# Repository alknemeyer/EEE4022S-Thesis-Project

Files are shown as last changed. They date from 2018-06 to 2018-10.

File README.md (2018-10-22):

# EEE4022S Thesis Project: Autonomous Object Identification and Tracking using Neural Networks

Git repository to backup work for my fourth year thesis project at the University of Cape Town. The repo is mostly just to back up my work across multiple work stations, so a lot of the commit descriptions are horrible. Woops.

## Abstract
Many systems require a camera to autonomously identify the objects in its field of view, and then rotate the camera to keep it aimed at a certain class of object.

This report describes the design and implementation of such a system on a low-powered
device. The system uses a Convolutional Neural Network to identify the position of
objects from photos, making use of a neural accelerator device to achieve near real-time
inferences. These measurements are improved through the use of a Kalman Filter, which
estimates the angular state of the tracked object. A multiprocess pipeline is used to
manage the control on a non-real time OS. Finally, a gimbal is designed and built to
rotate the unique payload.

The tracking system is shown to improve over a stationary camera setup.

## Coding style:

I find development using a notebook to be quite a bit easier than developing using a regular python file. Unfortunately, you can't import a `.ipynb` as a module. So, here's the workflow:
1. Use each `.ipynb` file to understand the code and make changes.
2. When you want to commit a change, click `Kernal > Restart and Clear Output` to remove your outputs + make the file a bit smaller (shows up as fewer lines in the git commit).
3. Run the command `jupyter nbconvert --to=python FILENAME.ipynb` to generate a `.py` file which can be imported as a module. Just make sure that any debugging code doesn't run if this is imported as a module into another file!

Alexander Knemeyer

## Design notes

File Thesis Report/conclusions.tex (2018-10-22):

\chapter{Conclusions}

Based on the test results shown in Chapter~\ref{chap:results} and discussion in Chapter~\ref{chap:discussion}, it can be conclusively said that the tracking camera system works better than a stationary camera setup. This is due to three main reasons:

First, the maximum field of view of the tracking system is significantly greater than that of a single stationary camera. One could use multiple stationary cameras, but this comes at a higher cost and extra work on the part of the researchers.

Second, the distortion which arises from setting the stationary cameras to wide-angle mode is significantly higher than the distortion from setting the tracking cameras to an narrow angle mode, which is made feasible by the tracking system. One could counter this buy purchasing even larger numbers of stationary cameras and setting each to the less distorting narrow field of view, but this comes at a higher cost and with extra work on the part of the researchers.

Third, there are other benefits to having a system which aims at a target which aren't practically feasible using a stationary camera setup. For instance, one could attach one or more distance sensors and a GPS to the gimbal to estimate the absolute location of the object.

When viewed as a general tracker in its own right, the system is not perfect and could see significant benefits given an extra week or two of time. The study was also not conclusive in that the tests in the laboratory alone aren't enough to empirically prove that the system could track a fast moving cheetah (given a neural network which can detect one) running close to the camera with a high perceived angular velocity.

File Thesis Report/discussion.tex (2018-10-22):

\chapter{Discussion}\label{chap:discussion}

Some things should be noted when considering the results shown previously.

The first is that, unless one decreased the effects of the image recognition latency, an angle between the cameras orientation and the object will always remain. This can be diminished if one has better knowledge of the animals movement prior to the experiment - for example, if it was known that the only thing being tracked is an object moving from left to right, the yaw Kalman Filter would be able to more reliably predict the current position of the object based on delayed data. This could result in better tracking, but comes with its own problems (such as overshoot if the object slows down, which is part of the RAM groups tests).

The second issue to discuss is that of the maximum angular range of the system, which is limited only by the wiring connecting the stationary part of the tracker to the rotating parts. While the tracker itself has a maximum angular rotation width of 175\textdegree, a portion of the field of view of the camera could be added to this to represent the total range that can be filmed. It may not make sense to add the full width, since part of the premise of the tracker is that object is aimed at directly.

Another topic is the tracking speed of the gimbal, and how it failed to track objects with high a velocity or acceleration. The Kalman Filters noise parameter can be adjusted to vary the state estimate from smoothness as a priority (which could be interpreted as seeing sudden changes in the sensed position as noise, which should be rejected) to robust tracking as a priority (where a sudden change in state is seen as the object moving quickly). In addition, the system would sometimes be unable to track a fast moving object simply due to the gimbals slower rotational rate, which wasn't investigated in time. It is unclear how much the Kalman Filter's parameters and gimbals slow movement limited the performance in this regard.

Finally, all of the tests were performed in a relatively confined space tracking close objects. It is unclear how well the tracker would perform tracking faster objects further away. Based on the results of this report, one could estimate its performance using the formula $\omega = v/r$, where $\omega$ is the rotational velocity, $v$ is the tangential angular velocity and $r$ is the distance to the object. Since the object tracker is confined to track objects at a certain maximum angular rate, but objects themselves move with linear velocities, as long as $\omega$ remains constant between tests on a human in a lab and a cheetah outdoors it is likely that the system would continue to track well.

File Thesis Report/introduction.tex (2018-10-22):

\chapter{Introduction}
This report details the research, design, implementation and testing of an automatic object detection and tracking system. It was made as a part of a final year undergraduate project.

\section{Background to the study}
For years, some researchers have turned to bio-mimicry for insight and inspiration into the design of robots. One such example is the University of Cape Town (UCT) mechatronics laboratory's Rapid Acceleration and Manoeuvrability group, which studies cheetahs with the aim of reproducing their extraordinary manoeuvrability in two and four legged robots \cite{website:uct_mechatronics}. To understand the dynamics of cheetah movement, they require footage of animals as they start and stop a sprint. A requirement of their research is that the cameras must be placed in pairs to achieve depth perception~\cite{website:depth_perception_from_stereo_camera}.

The researchers currently place multiple static cameras, with each pair covering a different area, in order to continuously film an animal through a full sprint. An illustration of this can be seen in Figure~\ref{fig:multiple_gopro_pairs}. \\

\begin{figure}[h!]
  \centering
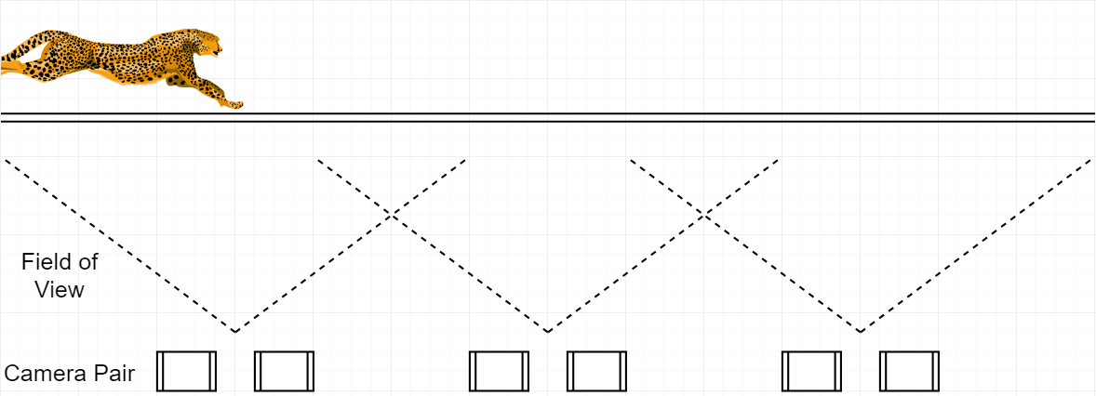
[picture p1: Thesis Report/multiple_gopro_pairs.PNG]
  
  \caption{\label{fig:multiple_gopro_pairs} An illustration of the camera set up in a typical animal movement study. Cheetah clipart from Change.org \cite{website:pic_of_cheetah}.}
\end{figure}

Unfortunately, this setup is not without its disadvantages: having multiple cameras requires extra setup time, effort into synchronizing the footage, money spent on equipment and extra work in keeping all devices charged. To maximise the time spent recording a sprint, the cameras are usually set to wide-angle mode. This introduces distortion into the recordings \cite{website:camera_distorion}.

This resulted in the following question: what if the cameras could instead rotate to track the cheetah as it moves? This way only a single pair of cameras would be required. An illustration of this in two moments of time is shown in Figure~\ref{fig:single_gopro_pair}.

\begin{figure}[h!]
  \centering
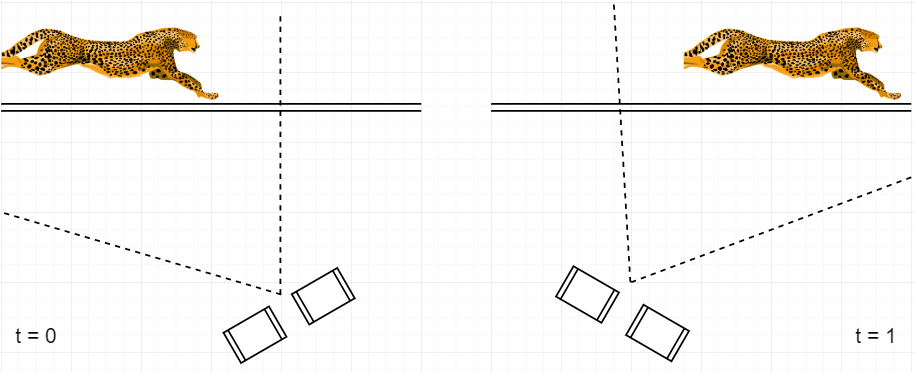
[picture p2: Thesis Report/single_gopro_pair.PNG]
  
  \caption{\label{fig:single_gopro_pair} The proposed solution: a single pair of cameras tracking an animal as it moves.}
\end{figure}

The researchers specified that such a tracking system should,

\begin{itemize}
	\item Not require a beacon, light or any other object to be placed on the object,
	\item Locate the object with high accuracy,
	\item Be able to differentiate between classes of objects, while treating different instances of the same class equally (in other words, locate \emph{any} cheetah regardless of its specific spot pattern),
	\item Have a low enough latency that the object can't escape the field of view of the cameras before a result is reached,
	\item Use a provided Raspberry Pi model 3 B as the main computing platform so as to remain mobile,
	\item Work robustly - this means locating the regardless of its orientation, lighting, specific shape, background, and so on - and finally,
	\item Be able to track any other object with minimal extra work or design required, should the focus of research be changed.
\end{itemize}

After comparing existing object tracking technologies, it was decided that the only way to robustly track the cheetahs in this scenario would be to use a neural network. This decision is elaborated on in section \ref{sec:compare_cv_techniques} of this report. The comparison showed that only machine learning techniques can accurately discriminate between a range of classes of objects using affordable and accessible sensing hardware alone (such as low-cost cameras).

\section{Other object tracking systems}
There are a large number of applications for a system which can track objects in real time using computer vision techniques. Some include:

\begin{itemize}
\item A robot which can sense nearby humans and make sure to not hurt them, or decide on a course of action which depends on the type of object in front of it.
\item A small autonomous airplane which patrols the skies above a national park, and broadcasts the location of any potential poachers that it finds.
\item A camera system which automatically tracks a ball or the centroid of the position all players, helping to record sports games.
\end{itemize}

Object tracking systems have already been incorporated into existing commercial products. One example is the "Mavic" drone from DJI, which can autonomously track humans \cite{website:DJI_mavic}. This allows people to launch the drone and have it autonomously follow them as they move around.

Another example is EyeCloud, a company that has developed a security system which covers a wider area than a single static camera could, and only sends an alert when it detects humans \cite{website:eyecloud}. This prevents false alarms from sounding when safe classes of objects, such as dogs, enter the field of view.

\section{Objectives of the study}
Based on the problem stated by the UCT researchers, the objective of the study is to design, build and test a system which can autonomously identify and track a fast-moving object using modern computer vision methods. A successful design would be able to rotate a pair of cameras to continuously aim at an object, track the object for longer than a stationary camera pair could, and not require the cameras to be set to distorting wide-angle modes.

Note that, while the ability to autonomously track an object has a wide range of applications, it is useful to limit oneself to a particular need in order to produce quantifiable 'success or failure' metrics. Thus, this project and report are mainly about solving a specific issue, with the premise that the project can be used for other applications with minimal modification. Discussions on literature and other applications will treat the system as a general purpose object tracker.

\section{Scope and limitations}
Due to the limited time and finances in an undergraduate thesis, testing the tracking system on actual cheetahs was not part of the agreed scope of this project. Instead, it was tested on moving humans in complex environments with the hope that this sufficiently mimics the scenario of tracking cheetahs (or any other fast-moving object) in the wild.

Additionally, the study was limited to tracking only one object in the frame at a time. This is because it is not immediately obvious what should be done when more than one object is present in the frame.

\section{Plan of development}
A development schedule was devised to decide how much time could be allotted for each component of the final system. It was as follows,

\begin{enumerate}
\item Create a rough design for the system as a whole to understand which skills and components would be necessary.
\item Spend a month learning relevant new theory, mostly in the field of computer vision.
\item Set up the main computing platforms, installing relevant software and testing the camera module, over the course of a week.
\item Optimize a cutting edge neural network for the specific scenario in this project over the course of two weeks. Failing that, choose an existing neural network architecture.
\item Compile the neural network and deploy it onto a neural accelerator stick, writing appropriate software, over the course of a week.
\item Use two weeks to design and 3D print a camera gimbal, and procure the necessary controller and actuators.
\item At the same time, rewrite the gimbal controller communication standard in python to allow the raspberry pi to send and receive commands.
\item Spend a week modelling the expected movement of the tracked object, and designing and implementing an appropriate Kalman Filter. Update this based on preliminary test results.
\item Spend two weeks implementing a parallel process-based data pipeline which takes a photo on the Pi camera, pre-processess it, passes it through the neural accelerator, retrieves the results, passes the results into the Kalman Filter and then commands the gimbal motors to re-orient the camera appropriately. 
\item Test final the system over the course of a week, tweaking the design based on results.
\item Use the last three weeks to write a report which summarizes the entire project, based on small notes taken during the course of the project.
\end{enumerate}

\section{Report outline}

The report begins with a review of the current literature surrounding object tracking. As the system combines a number of technologies, it also presents previous knowledge on all of the components which ultimately formed a part of final system.

Next, a more detailed description of the problem, plan of action, activities and project timeline are provided.

Following that are a few chapters which discuss the actual methodology used in the design and implementation of the tracking system. This is done with the aim that reproducing and extending the project can be done with minimal effort.

The results of testing the system are then shown.

Finally, the report ends off with conclusions on the project's success or failure, along with recommendations for future work.

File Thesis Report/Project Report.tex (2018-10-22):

\documentclass[a4paper,12pt]{report}

\usepackage[top = 1in, bottom = 1in, left = 1in, right = 1in]{geometry}
\usepackage{graphicx}
\usepackage{fancyhdr}
\usepackage{amsmath, amsthm, amssymb}
\usepackage{lastpage}
%\usepackage{subfigure}
\usepackage{lscape}
\usepackage{hyphenat}
\usepackage{setspace}
\usepackage{hyperref}  % used for \href and urls in .bib
\usepackage{xcolor}  % use to colour text
\usepackage{subfig}  % putting packages side by side
\usepackage{textcomp} % degree symbol

%\usepackage{listings}
\usepackage{pythonhighlight}
%\begin{python}
%x = 1
%\end{python}
%\pyth{__init__}

\usepackage{sectsty} % adjust size of chapter headings
\chapternumberfont{\large}
\chaptertitlefont{\Huge}

\usepackage{wrapfig} % wrap text around figures
%\begin{wrapfigure}{R}{5.5cm}
%\caption{A wrapped figure going nicely inside the text.}\label{wrap-fig:box_around_blossom}
%\includegraphics[width=5.5cm]{methodology/box_around_blossom}
%\end{wrapfigure}

\usepackage{titlesec} % decrease the whitespace at chapter start
\titleformat{\chapter}[display]
{\normalfont\large\bfseries}{\chaptertitlename\ \thechapter}{0pt}{\Huge}
\titlespacing*{\chapter}{0pt}{-40pt}{5pt}
%	  {shift right/left}, {up/down}, {between title and text}

%\usepackage{animate} % embed videos

% add lines by header and footer
%\usepackage{titleps}
%\newpagestyle{ruled}
%{\sethead{}{Header}{}\headrule
%  \setfoot{}{Footer}{}\footrule}
%\pagestyle{ruled}

%%%%%%%%%%%%%%%%%%%%%%%%%%%%%%%%%%%%%%%%%%%%%%%%%%%%%%%%%%%%%%%%%%%%%%%%

% page formatting
\parskip = 4mm
\parindent = 0mm
\renewcommand{\headrulewidth}{0.4pt}
\rhead[]{\thesection}
\lhead[\thechapter]{}

%%%%%%%%%%%%%%%%%%%%%%%%%%%%%%%%%%%%%%%%%%%%%%%%%%%%%%%%%%%%%%%%%%%%%%%%

\begin{document}

\thispagestyle{empty}
{\Huge \begin{center}
Autonomous Object Identification and Tracking using Neural Networks% title
\hrule
%{\Large ya boi} % subtitle
\end{center}}

\vskip 5mm
\begin{center}
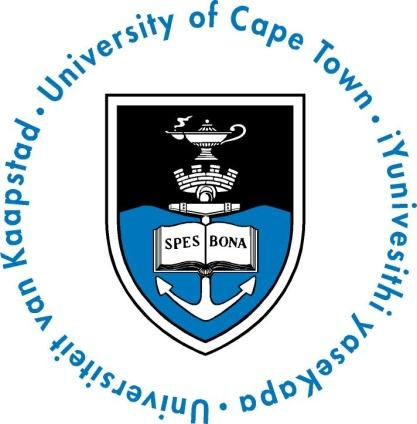
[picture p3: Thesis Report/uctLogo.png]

\end{center}

\vskip 5mm
\begin{center}
\textbf{Presented by:}\\
Alexander Lutz Knemeyer\\
KNMALE002\\
Department of Electrical and Electronics Engineering\\
University of Cape Town
\end{center}

\vskip 10mm
\begin{center}
\textbf{Prepared for:}\\
Callen Fisher and Edward Boje \\
Department of Electrical and Electronics Engineering\\
University of Cape Town
\end{center}

\vskip 10mm
\begin{center}
Submitted to the Department of Electrical Engineering at the University of Cape Town in partial fulfilment of the academic requirements for a Bachelor of Science degree in Mechatronics Engineering
\end{center}

\vskip 5mm
\begin{center}{\bf \today}\end{center}

{\centering
\textbf{Key words:} object tracking, autonomous, neural network, Kalman Filter, multiprocess}

\newpage

%\thispagestyle{empty}  % leave a blank page
%\mbox{}
%\newpage

\onehalfspacing
\nohyphens{
\thispagestyle{empty}
\vskip 40mm

% Please leave the declaration as it is (Standard UCT declaration).
{\Large Declaration} \\
\hrule

\vskip 10mm
\begin{enumerate}
\item I know that plagiarism is wrong. Plagiarism is to use another's work and pretend that it is one's own.
\item I have used the IEEE convention for citation and referencing. Each contribution to, and quotation in, this report from the work(s) of other people has been attributed, and has been cited and referenced.
\item This report is my own work.
\item I have not allowed, and will not allow, anyone to copy my work with the intention of passing it off as their own work or part thereof.
\end{enumerate}

\vskip 10mm
Signature: \ldots\ldots\ldots\ldots\ldots\ldots\ldots\ldots\ldots
\\A. L. Knemeyer
\vskip10mm
Date: \ldots\ldots\ldots\ldots\ldots\ldots\ldots\ldots\ldots\ldots

\fancyfoot[C]{\thepage}
\pagestyle{plain}
\newpage

\pagenumbering{roman}
{\Large Acknowledgements} \\
\hrule

A number of people were immensely helpful in the undertaking of this project.

Callen, thank you for your guidance, encouragement and supervision.

Justin, thank for your endless patience and advice whenever I came with questions or asking for a favour.

Stacey, thank you for laser cutting components for the gimbal. You're far too nice.

Neil, thank for proofreading an earlier version of this report. Your input was highly appreciated and raised the quality of my writing.

Sylvan, your friendship during this trying time truly saved my sanity. I'll always fondly remember working in the lab with you.

My family, your confidence in me and my abilities greatly helped keep my ambitions high and stress at a manageable level.

Sophia, thank you for your endless support and encouragement. I don't handle stress very well so our little chats helped a lot with my sanity.

\newpage

\include{abstract}

{\Large Abbreviations and Initialisms} \\
\hrule
\begin{table}[h!]
	\centering
	\begin{tabular}{p{2cm} p{0.1cm} p{15cm}}
	FOV & & Field Of View \\
	CNN & & Convolutional Neural Network \\
	NCS & & Neural Compute Stick \\
	OS  & & Operating System \\
	VM  & & Virtual Machine \\
	CPU & & Central Processing Unit \\
	GPU & & Graphics Processing Unit
	\end{tabular}
\end{table}

\newpage

\tableofcontents

\newpage
\listoffigures

% Page formatting, to place section titles as headers of odd pages and Chapter titles as headers of even pages.
\newpage
\fancyhead[RE,LO]{}
\fancyhead[LE]{\leftmark}
\fancyhead[RO]{\rightmark}
\pagestyle{fancy}

\pagenumbering{arabic}

%%%%%%%%%%%%%%%%%%%%%%%%%%%%%%%%%%%%%%%%%%%%%%%%%%%%%%%%%%%%%%%%%%%%%%%%

\include{introduction}
\include{literature_review/literature_review}
\include{literature_review/lit_nn}
\include{literature_review/lit_EKF}
\include{literature_review/lit_gimbal}
%\include{literature_review/lit_controller}
%\include{research_design_and_timeline}
%\include{Methodology}
%\include{methodology/meth_system}
\include{methodology/meth_nn}
\include{methodology/meth_EKF}
\include{methodology/meth_gimbal}
\include{methodology/meth_control}
\include{results/results}
\include{discussion}
\include{conclusions}
\include{recommendations}
%\include{References}
%\appendix
\chapter{Appendix}
The authors submission into the SAIEEE NSPC:

\href{https://www.youtube.com/watch?v=NjCOmwhG3zo}{\pyth{https://www.youtube.com/watch?v=NjCOmwhG3zo}}
\\

Two videos which compare the stationary and tracking cameras:

\href{https://youtu.be/Oea_mKTjV5U}{\pyth{https://youtu.be/Oea_mKTjV5U}}
\\

The GitHub page containing all code:

\href{https://github.com/alknemeyer/EEE4022S-Thesis-Project}{\pyth{https://github.com/alknemeyer/EEE4022S-Thesis-Project}}

\newpage

\bibliographystyle{IEEEtran}
%\bibliographystyle{plain}
\bibliography{references}

}
\end{document}

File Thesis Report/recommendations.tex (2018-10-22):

\chapter{Recommendations}

There are a number of alternative ideas and approaches which merit investigation. The ideas were left unimplemented as they were realised too late in the process or would have required too much time or money.

The list of future recommendations is as follows:

\begin{enumerate}
	\item Instead of tracking the state of the object as an angle, try instead track it as an $(x,~y)$ position on a plane surrounding the tracker. This would either require a depth estimating neural network or a distance sensor which works even when the system doesn't aim directly at the object.
	\item Get a camera, computer and neural accelerator which decrease the total sensing latency.
	\item Consider adding an encoder to the gimbal to avoid built up gyroscope drift when an accelerometer axis lines up with with a rotation axis.
	\item Consider switching the main programming language from python to something faster and better oriented to parallelism. The language could also be low-level, now that most of the debugging and prototyping has already been done.
	\item After the network selection process occurred in this project, the TinyYOLO architecture was added to the list of models officially supported by the Movidius NCS. TinyYOLO has some grand claims about its speed, so it should be evaluated as option for future work. Reducing the latency in the system would make the overall project significantly easier.
\end{enumerate}

%Bad things from gimbal: hard to make screws firm+they come loose, didn't make a nice way of keeping cameras inside frame, didn't make nice spot to put pi and gimbal controller.

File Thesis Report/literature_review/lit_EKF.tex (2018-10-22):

\section{The Kalman Filter}

While object detection algorithms operate at rates of less than 10 Hz when run on the Movidius NCS, the controller for a rotating camera necessitates a higher frequency. In addition, it would be useful to be able to estimate a likely position for the object in cases where the object detection algorithm fails.

The Kalman Filter (and its nonlinear variant, the Extended Kalman Filter), can solve both of these problems \cite{kalman1960new}.

\subsection{An brief introduction to the Kalman Filter}
A Kalman Filter is an algorithm used to estimate the state of a linear system ($\hat{x}$) along with the uncertainty of the estimate ($P$) based on measurements over time ($z$). The measurements are assumed to include noise with covariance $R$. It makes use of a model ($F$) which represents the dynamics of the system ($\hat{x}_{k} = F\hat{x}_{k-1}$), along with a matrix which represents inaccuracies in the model, dubbed 'process noise' ($Q$) and measured factors which affect the state, but aren't part of the current set of states ($u$). It takes into account the sensor scaling which maps between sensor measurements and state values ($H$). The notation for Kalman Filters has not been totally standardised.

A variety of excellent resources exist which explain the deeper intuition behind the Kalman Filter \cite{website:wlu_kalman_tutorial, website:bzarg_kalman_tutorial}. Thus, only the equations and high-level concepts which are absolutely necessary will be discussed in this chapter.

Kalman Filters continuously alternate between a predict stage and an update stage. In the predict stage, the Kalman Filter uses a model of the system and known disturbances to update the state estimate and uncertainty estimate. These are represented by the equations,

\[ \hat{x}_k = F_k \hat{x}_{k-1} + B_k u_k \]
\[ P_k = F_k P_{k-1} F_k^T + Q_k \]

The $k$ subscripts denote the point in time at which the calculation takes place. This means that any matrix in the algorithm could be updated as time goes on.

In the 'update' stage, the Kalman Filter makes use of a model of uncertainty estimates to produce a new state estimate which is a trade-off between new data from a sensor, and the state estimate produced by the predict stage.

\[ \hat{x}_k = \hat{x}_{k-1} + K_k (z_k - H_k \hat{x}_{k-1}) \]
\[ P_k = (I - K_k H_k) P_{k-1} \]

where the Kalman gain $K$ at a time $k$ is calculated as,
\[ K_k = P_k H_k^T (H_k P_k H_k^T + R_k)^{-1} \]

%These stages are alternated as \emph{predict} $\rightarrow$ \emph{update} $\rightarrow$ \emph{predict} $\rightarrow$ \dots
As an illustration, consider the extremes during the update stage: when $K = 0$, we have

\[ \hat{x}_k = \hat{x}_{k-1} + 0 (z_k - H_k \hat{x}_{k-1}) = \hat{x}_{k-1} \]

If $H_k = 1$ and $K = 1$, we have

\[ \hat{x}_k = \hat{x}_{k-1} + (z_k - \hat{x}_{k-1}) = z_k \]

Values of $K$ in between result in a state update which is some combination of the sensed values and modelled dynamics of the system. The Kalman Filter selects this combination based on its estimate of the mean and variance of the state estimate and measurement. An illustration of this is shown below, in Figure~\ref{fig:kalman_filter_loop}.

\begin{figure}[h!]
  \centering
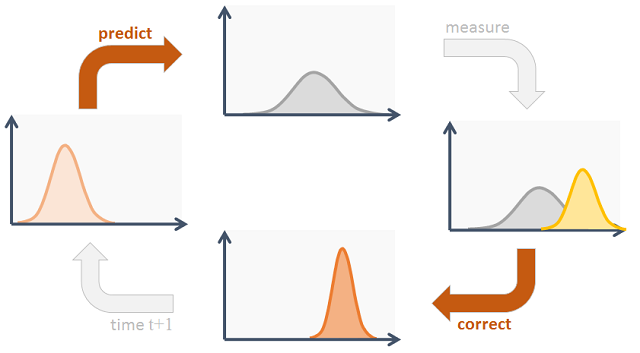
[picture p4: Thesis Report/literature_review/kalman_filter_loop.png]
  
  \caption{\label{fig:kalman_filter_loop}An illustration showing how the mean and covariance of an estimate (as predicted by the Kalman Filter) changes during the predict and update stages \cite{website:kalman_visualisation}.}
\end{figure}

Finally, given a Kalman Filter with an accurate estimation of the systems state and a model which adequately predicts the future state of the system, one can interpolate between readings from a sensor with slow update rates by making use of the prediction model $F$. This could mean getting model updates at a required speed of 20 Hz using a sensor which only makes measurements at a rate of 5 Hz.

\subsection{An introduction to the Extended Kalman Filter}
An Extended Kalman Filter (EKF) is simply a nonlinear version of a Kalman Filter, where the transition from estimated state $\hat{x}_{k-1}$ to state $\hat{x}_k$ is some nonlinear mapping $f(x)$ and/or the mapping from state values to sensor values is a nonlinear function $h(x)$. It works by using a Taylor approximation to linearize about an estimate of the current mean and covariance. This also results in differing values for the sensors Jacobian, $H~=~\frac{\delta h}{\delta x}$.

\[ F \hat{x} \rightarrow f(\hat{x}) \qquad H \hat{x} \rightarrow h(\hat{x}) \]

To understand the effects of this, consider the following: given a sensor which maps from state to measurement following the function $h(x) = x^2 - 10\cos{(x)}$, reading a value of $x = 8.5$ when the state was actually $x=7.5$ would result in an absolute error of $25.5$. However, reading a value of $x=4.5$ when the state was actually $x=3.5$ would result in an absolute error of $0.743$. Clearly, the same one unit error (due to noise, for example) should be treated differently depending on where it happens on the sensor curve. The EKF does just this! Code to create the plot can be found on the authors \href{https://github.com/alknemeyer/EEE4022S-Thesis-Project/blob/master/Final%20code/Illustrations%20for%20report.ipynb}{GitHub repository}.

\begin{figure}[h!]
  \centering
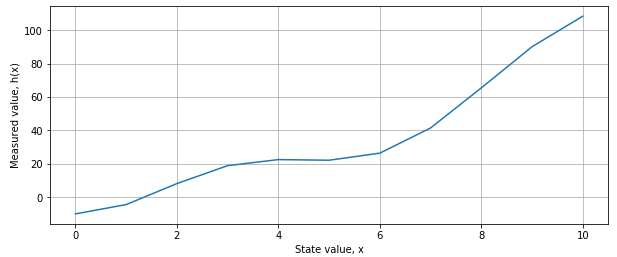
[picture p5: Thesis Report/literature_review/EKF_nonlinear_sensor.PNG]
  
  \caption{\label{fig:EKF_nonlinear_sensor}A plot of a hypothetical nonlinear sensor which maps state to measured value according to the function $h(x) = x^2 - 10\cos{(x)}$.}
\end{figure}

Thus, an EKF would update its covariance estimates in a different way depending on the part of the sensor/prediction curve it finds itself on. Implementation-wise, the only difference between the linear and non-linear variants of the Kalman Filter is that the state transition and observation models can be non-linear differentiable functions with a constantly updating sensor Jacobian.

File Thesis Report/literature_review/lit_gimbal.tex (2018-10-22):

\section{The camera gimbal}
A gimbal is device which can rotate about one or more axis \cite{website:definition_gimbal}. A typical use is to place a camera and 3 actuators on a gimbal, resulting in the ability to rotate the camera in the roll, pitch and yaw axis. An annotated render of this can be found in Figure~\ref{fig:roll_pitch_yaw_camera}.

\begin{figure}[h!]
  \centering
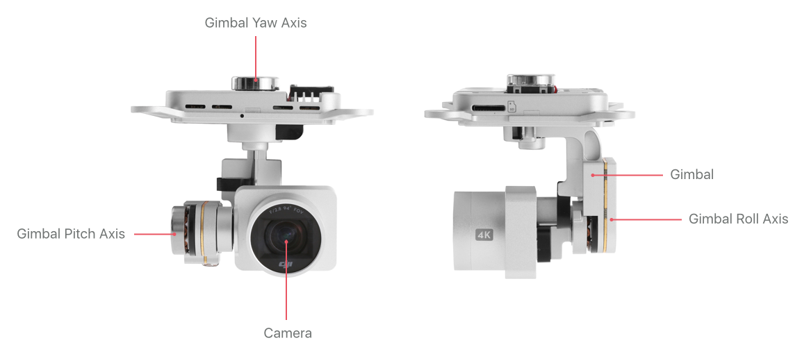
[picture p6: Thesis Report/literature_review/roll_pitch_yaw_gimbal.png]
  
  \caption{\label{fig:roll_pitch_yaw_camera} An illustration of the roll, pitch and yaw axis used in a gimbal~\cite{roll_pitch_yaw_camera}.}
\end{figure}

While gimbal designs are \emph{fairly} standard, a few critical design choices must be made when building or buying one.% The rest of this chapter will detail some of the options available.

\subsection{Comparison of actuator types}\label{ssec:gimbal_comparison}
The type of actuator used in the gimbal has a significant effect on the design of the gimbal (due to actuator shape), the speed it can move, the camera weight it can handle and quality of the resulting photos and videos (due to actuator vibrations). Thus, three relevant actuator types (a brushed DC motor, a servomotor and a BLDC motor) were considered and compared, taking into account the selection available at local stores.

To make the comparison more concrete, specific possible models were chosen. The DC (Direct Current) motor considered was 99:1 Metal Gearmotor available from Pololu.com \cite{DC_motor_choice}. The servo motor was a 20kg.cm Metal Gear Servo available from Robotics.org.za \cite{servo_motor_choice}. Finally, the Brushless DC (BLDC) motor was a Quanum 2208 brushless gimbal motor \cite{bldc_motor_choice} available second hand.

The DC motor is relatively long and heavy. It also requires an additional H-bridge circuit to drive it. Finally, it wasn't clear how the Raspberry Pi (running a non realtime OS) would use the rotational decoder and apply a control law.

The servo motor is relatively easy to use as the Raspberry Pi has built in PWM. It also has relatively high torque. However, it too is relatively large and would likely move in a jittery fashion, resulting in lower quality footage.

Lastly, the BLDC motor is potentially expensive and quite complex to use. Its advantages are its was compactness, low weight and high speed. It is worth noting that, while controlling BLDC motors can be fairly complex, using a store-bought controller allows for one to easily leverage off the design work of other engineers. This results in a faster, smoother and more stable gimbal than one could build in a short period of time.

\subsection{\label{ssec:gimbal_design_inspirations}Gimbal design inspirations}
It is useful to review existing gimbal designs in order to avoid unnecessary re-invention of the wheel. Luckily, a large number of designs are available on the internet. One design which stood out from the research phase was \href{https://www.thingiverse.com}{thingiverse.com} member Velocirotor's clever gimbal design, dubbed the \href{https://www.thingiverse.com/thing:2804872}{Primbal Session} \cite{website:primbal_session}. It is light-weight, simple to 3D print and has an easy method to adjust length to balance the gimbal's three axis. A render of the design can be found in Figure~\ref{fig:primbal_pic}.

\begin{figure}[h!]
  \centering
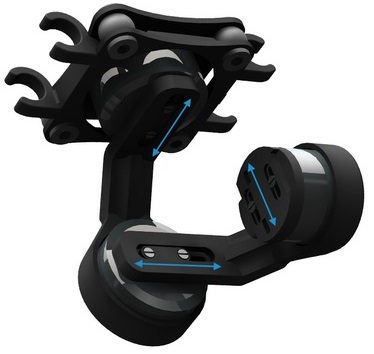
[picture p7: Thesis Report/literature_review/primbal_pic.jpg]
  
  \caption{\label{fig:primbal_pic} A render of the Primbal Session gimbal design.}
\end{figure}

Some inspiration was also taken from a gimbal designed by mechatronics engineering student Sylvan Morris, made during a period of vacation work. Noteworthy characteristics include the two-plate shock absorption system and method of mounting onto a quadcopter. A photo of his design can be found in Figure~\ref{fig:sylvan_gimbal}.

\begin{figure}[ht!]
  \centering
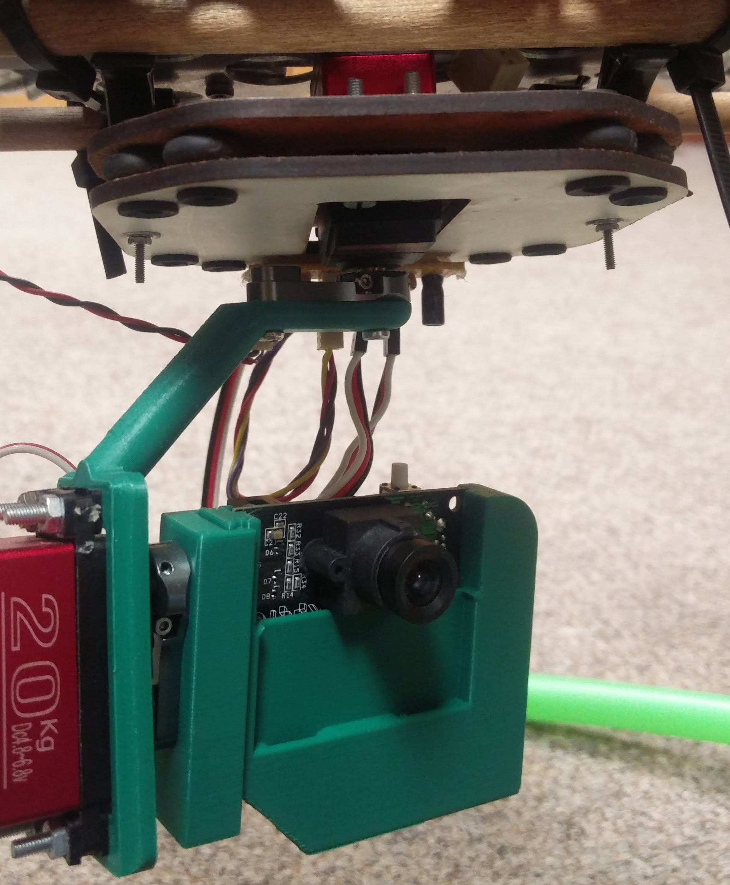
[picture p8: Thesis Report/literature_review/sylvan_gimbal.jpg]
  
  \caption{\label{fig:sylvan_gimbal} A photo of Sylvan Morris's gimbal design.}
\end{figure}

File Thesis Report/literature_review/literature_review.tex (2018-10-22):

\chapter{Literature Review}

The design of a real time object tracker on a low-power computer necessitates several systems, including object detection, a camera gimbal and a Kalman Filter. The literature relevant to these systems are covered in more detail in this chapter.

\section{An overview of real time computer vision based automatic tracking systems}\label{sec:compare_cv_techniques}
The mechatronics RAM group researchers required a system which can track an object using a camera and computer vision techniques alone. That requirement is somewhat heavy on jargon, but it can be unpacked as follows:

\textit{Track: follow the trail or movements of (someone or something), typically in order to find them or note their course \cite{website:definition_track}.}
%
A number of systems which interact with the world must track an object. To give some examples, in our daily lives we as humans visually track other cars when driving, keep an idea of our geographic location and estimate the position and velocity of people as they walk so we don't bump into them. Examples more relevant to this project include pointing camera at a ball during a sports match and tracking poachers from the air in a game park.

\textit{Automatic: working by itself with little or no direct human control \cite{website:definition_automation}.}
%
A human could (in principal) manually track an object using their own vision and natural object-recognition ability. However, this isn't feasible for all applications: this type of job can be fairly boring, resulting in the human losing concentration over time. Another issue is that the human should be paid to perform this task if it is their job. This completely excludes all applications which must have a low running cost.

In contrast, autonomous tracking systems require little to no ongoing human work - as a result, they tend to have vastly reduced running costs with higher reliability over long run times \cite{website:BCG_automation}.

\textit{Real time: relating to a system in which input data is processed within milliseconds so that it is available virtually immediately as feedback to the process from which it is coming, e.g. in a guidance system \cite{website:definition_real_time}.}
%
Not all tracking systems can (or need to) run in real time. For example, one might film a moving object and then automatically locate the objects position in the video offline. However, certain systems must track an object in real time so as to be able to (for example) orient a camera to point at the object, or result in some other immediate response.

\textit{Computer-vision: a field of computer science that works on enabling computers to see, identify and process images in the same way that human vision does \cite{website:definition_computer_vision}.}
%
Some tracking systems require a device to be placed on the object being tracked. Some still require a camera - for example, one could place an infra-red beacon on the object and pair it with a camera with an appropriate lens \cite{koyuncu2010survey}. Others involve no cameras, and instead use embedded sensors alone (such as GPS, accelerometers and gyroscope) \cite{sakpere2017state}. Again, while this may be acceptable for some systems, it comes at a cost: some sort of device must be placed on the object. If the object is a cheetah, this could cause a disturbance to the animals behaviour. The device must be kept charged, so periodic interference with the object is required. Physical contact must be made with the object to install the tracker - this isn't always possible.

In contrast, object tracking based on computer vision doesn't require any device to be placed on the object. This is far more scalable, as the same system can track more objects without any additional hardware. Embedded tracker based systems require an additional piece of hardware for every object being tracked.

However, these benefits come at a cost: the object must be close enough to the camera system that the object can be recognised. In contrast, an embedded GPS, IMU and radio system could track objects to the range of the radio system, provided at GPS lock can be achieved.

%https://en.wikipedia.org/wiki/Infra-red_search_and_track
There are other vision-based systems which don't use computer-vision techniques. For example, infra-red tracking systems don't usually differentiate between classes of objects, but instead track any movement in the frame \cite{sakpere2017state}. These systems are often relatively cheap, but since they can't differentiate between types of objects, they don't work for all scenarios. Another issue is that heat-based systems stop working when the external temperature is the same as the temperature of the object being tracked. This is an issue for a system which might track a human with a body temperature of 37.5\textdegree{} in 37\textdegree{} weather.

Finally, there are other systems which can track objects without embedding a tracker or using vision. Technologies like radar can send off a ping and then build a view of the environment based on the returning signal \cite{sakpere2017state}. Radar tends to give good range (significantly further than vision would give), but struggles to differentiate between types of objects very well. For example, a radar system \emph{might} be able to differentiate between a car and a human from 1km away, but not human from a dog or car from elephant. It also doesn't work well at closer distances, and often has a prohibitive cost.

Of course, there are reasons for and against the use of each of these technologies. These should be considered before deciding on a particular approach for a given project.

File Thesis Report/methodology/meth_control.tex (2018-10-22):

\chapter{Control Loop Design and\\Implementation}
This chapter details the process of combining the project components mentioned in previous chapters. This was surprisingly non-trivial due to the high latency of the object detector and need for parallelization.

\section{Description of software implementation}
The main negative consequence of choosing a CNN for object detection is the latency introduced by the long inference time. This influenced the system design to a great extent. In addition, the unexpectedly long time required to get a photo from the Pi camera and preprocess it added to the list of compute-intensive latency-causing components. Thus, it was decided that the system would make use of multiprocessing and message passing, made possible and simple through the use of python's built in \pyth{multiprocessing} module.

This helped in two ways: the first is that it freed the main process to continuously send commands to the gimbal using the estimate from the KF. It would simply not be tolerable to be out of this loop for 200ms or more while a photo is taken and the result inferred.

The second advantage is that while implementing a parallel data pipeline would increase the overall latency between a photo being taken and the result being used, the number of readings per second actually increases. This is because while one process takes a photo, another can simultaneously infer the image while the parent process communicates with the gimbal controller. This meant that a single faulty or missing measurement would quickly be replaced by a new one.

Thus, data was passed from one process to the next using parallel processing Queues. A block diagram of this and the other components in the pipeline is shown in Figure~\ref{fig:system_block_diagram}.

\begin{figure}[h!]
  \centering
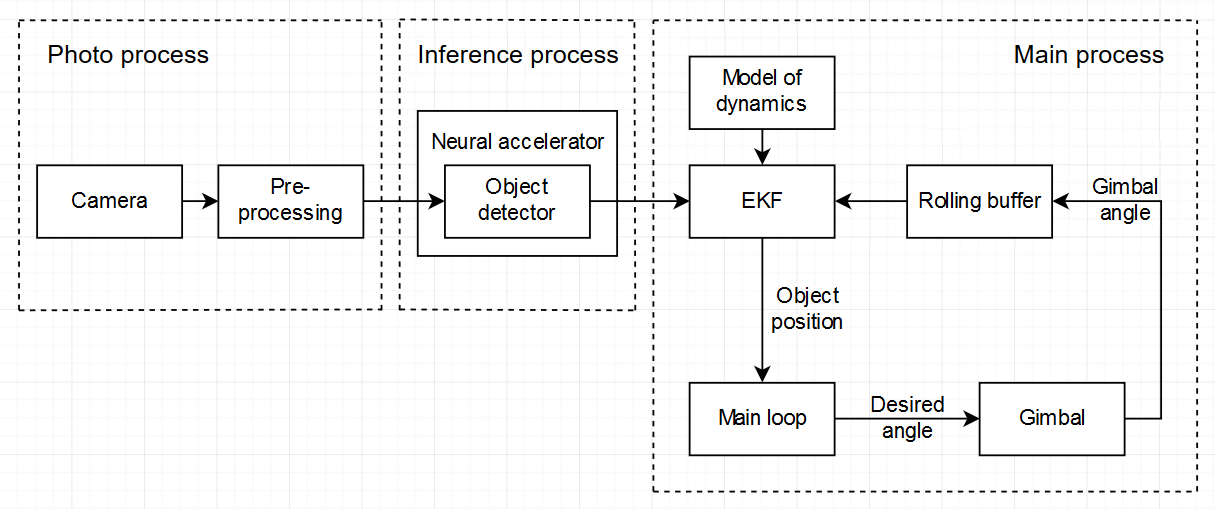
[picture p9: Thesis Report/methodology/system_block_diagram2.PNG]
  
  \caption{\label{fig:system_block_diagram}A block diagram of the flow of data through the system, showing the functions of each process.}
\end{figure}

A more detailed description of the rest of the general flow diagram and the reasoning behind the choices made is detailed in the following subsections.

\subsection{The photo process}
In the photo stage, a child process would interface with the Raspberry Pi camera. It received all photos taken, did some preprocessing on each image, and then passed the resulting array to the next stage in the pipeline. It also sent the time at which the photo was taken. A single loop in this stage took around 60-150ms, depending on the chosen camera resolution.

\subsection{The inference process}
In the inference stage, another child process interfaced with the Movidius NCS. It received the preprocessed images from the previous stage and loaded them onto the neural accelerator. While waiting for the inference result, it would occasionally save a copy of the photo to disk for offline debugging purposes. Once it received the result, it would decode the neural net output, put it and the photo time into an easy to use python dictionary and place it in a final buffer. Again, this needed to be in a separate process as the total time required to pass an image to the NCS and then infer a result was about 100ms.

\subsection{The main process}
While this was happening, the main parent process continuously ran a control loop which received the results from the inference process, and used it to update two Kalman Filters which track the object's pitch and yaw states. It also communicated with the gimbal controller using its serial API. Lastly, it logged relevant data for debugging purposes.

\section{Fixing timing issues}
The large latency in the object detection caused further problems which needed to be fixed. These problems and their solutions are described in the following subsections.

\subsection{Inference result/gimbal state timing issues}
Recall that the neural network can only give a relative angle between the camera and the object, while the gimbal works using absolute angles with respect to some initial position.

The Kalman Filters, each tracking the absolute angular states of the object, would need to be passed the results from the neural network as absolute angles. This could be done by reading requesting the gimbal to send its angular position at the time that the photo was taken. \\

\begin{python}
camera_angle = gc.get_motor_angles()
KF_yaw.update(angle_to_object_yaw + camera_angle['yaw'])
KF_pitch.update(angle_to_object_pitch + camera_angle['pitch'])
\end{python}

However, this presented a new problem to be solved - the angular state of the camera at the time that the photo was taken usually significantly different by the time the result had been inferred due to the large latency in the inference.

\begin{enumerate}
\item $t = 0$: photo taken and inference started.
\item $t = 200ms$: result received for for $t=0$. By this time, the gimbal has moved slightly, causing a mismatch between the relative angles from the recent inference and the current absolute gimbal angles.
\end{enumerate}

The solution was to keep a rolling buffer of a few gimbal angle readings, and then use the angle measurement at the time closest to the photo time to properly convert the neural network measurement from a relative angle to a global one. The snippets of code relevant to this are shown below. \\

\begin{python}
# gc_angles is the dictionary returned from gc.get_motor_angles()
def log(self, gc_angles):
	self.time_buffer[self.idx % self.buffer_len] = time.time()
	self.yaw_buffer[self.idx % self.buffer_len] = gc_angles['yaw']
	self.pitch_buffer[self.idx % self.buffer_len] = gc_angles['pitch']
	self.idx += 1

def angle_closest_to(self, photo_time):
    # index of time closest to the photo time
    idx = np.argmin(np.abs(self.time_buffer - photo_time))
    return self.yaw_buffer[idx], self.pitch_buffer[idx]

# log angle of gimbal
gimbal_buffer.log(gc.get_motor_angles())

# later on, when a result arrived from the neural network:
obj_yaw, obj_pitch, photo_time = get_angles_and_photo_time_from_nn()
logger_yaw, logger_pitch = gimbal_buffer.angle_closest_to(photo_time)
EKF_yaw.update(obj_yaw + logger_yaw)
EKF_pitch.update(obj_pitch + logger_pitch)
\end{python}

Another reason why this approach was necessary was because the time between taking a photo and getting the result was non-constant.

\subsection{Control timing issues}
Given that the KF in the gimbal was working correctly, there were two options for how to handle the latency of the pipeline.

\begin{enumerate}
\item $t = 0$: photo taken and inference started.
\item $t = 200ms$: result received for for $t=0$. By this time, the object has moved slightly.
\item Two options to move the gimbal at $t=200ms$:
	\begin{itemize}
	\item Use the KF estimate using measurements from $t\le0$.
	\item Use the KF to predict from $t=0$ to $t=200ms$
	\end{itemize}
\end{enumerate}

The first approach was to track the KFs estimate of the object at all times. Since the KFs receive all data with a roughly $\approx 200ms$ delay, the resulting system would essentially track the position of tracked object $200ms$ in the past. This approach accepts the fact that the camera will usually not aim at the camera but instead lag a few degrees behind it (depending on the angular velocity of the object).

The second approach would be to use the KF estimate of the angular state of the object to 'predict' from the KF's $\approx 200ms$ lagging time into the actual live time. If successful, the camera would perfectly track the position of the object as it moves along. However, there is no guarantee that the KF prediction will match the actual movements of the object. Thus, this approach would be prone to things like extreme overshoot every time the object slowed down or turned around.

There is merit to both approaches - the first is more robust, with worse camera tracking. The second is less robust, but would result if better footage if the object moved at a relatively constant velocity. Thus, the choice depends largely on application. For the purposes of this project, robustness was valued more highly. This meant going with the first approach of tracking the object a fifth of a second in the past.

\section{Benchmarking the flow of data}
Due to the non real time OS on the Raspberry Pi, timing each part of the data pipeline resulting in varying results. What follows are average timed values:

\begin{itemize}
\item Time to take a photo: 40 - 120 ms.
\item Time to pre-process the photo: 5 - 15ms.
\item Time to upload the photo to the NCS: 15 - 20ms.
\item Time to infer a result: 80 ms.
\item Time to decode the result: $<$ 1ms
\end{itemize}

There were also synchronization issues wherein the time between one process placing data in a queue and it being fetched by the next process was not negligible.

In total, the time from photo to results was usually 200 - 300ms

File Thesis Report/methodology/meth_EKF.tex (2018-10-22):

\chapter{Kalman Filter Modelling and Design}

The still fairly low update rate of the object detector (as mentioned in Subsection~\ref{ssec:meth_nn_performance_increase}) necessitated the use of a Kalman Filter to both increase the reliability of the measurements and to get a better estimate of the object's state in between measurements.

There were a number of design decisions which had to be made when modelling the system and implementing the filter. These are discussed in this chapter, as well as some simulation and testing results.

\section{System modelling}
A Kalman Filter (KF) was used to estimate the state of the tracked object as it moved around. Since the camera system generally rotates around an axis and there is no reliable estimate of the distance from the camera to the object being tracked, it was decided that the state would be measured in absolute angular coordinates.

A model of the dynamics of the tracked object had to be chosen for the KF to operate optimally. However, there is no possible "correct" model for the movements of the object being tracked (for example, a cheetah won't stick to the rule of moving at a constant velocity) and no way to estimate the disturbances $u$ which may effect its decision to change its velocity. Thus, it was decided that the model would make the incorrect assumption that the object would either maintain a constant velocity, constant acceleration or exponentially decaying acceleration. These three approaches needed to be tested, with the best being used in the final model.

This resulted in the global angular position, velocity and acceleration of the tracked object being estimated. These were stored in the state matrix $x$ as,

\[ x = \begin{bmatrix} \theta \\ \dot{\theta} \\ \ddot{\theta} \end{bmatrix} \]

These states are related through integration, where $\theta = \int{\dot{\theta} dt} = \int{\int{\ddot{\theta} dt}dt}$. They can be approximated using the discrete integration formulae, $\dot{\theta}_k = \dot{\theta}_{k-1} + \Delta T \ddot{\theta}_{k-1}$ and $\theta_k = \theta_{k-1} + \Delta T \dot{\theta}_{k-1}$. The prediction matrix was thus chosen as,

\[ F = \begin{bmatrix} 1 & \Delta T & 0 \\
                       0 & 1 & \Delta T \\
					   0 & 0 & \beta
		\end{bmatrix} \]

where $\beta$ is a factor which could be $\beta = 1$ for constant acceleration ($a_i = a_{i-1}$ in the predict stage), $0 < \beta < 1$ for decaying accelerating (for example, $a_i = 0.9 a_{i-1}$) or $\beta = 0$ for no acceleration. This was done to ensure quick and easy prototyping.

Next, the sensor needed to be added. The neural network returns the coordinates of the position of the object, measured in pixels. For the sake of modularity and simpler math, the pixel range of \pyth{pixel} $\in$ \pyth{[0, 299]} along a single axis was normalized to a value \pyth{pixel_norm} $\in$ \pyth{[-1, 1]}, with a pixel value of zero corresponding to the centre of the image. An illustration of this is shown below, in Figure~\ref{fig:pixel_to_angle}.

\begin{figure}[h!]
  \centering
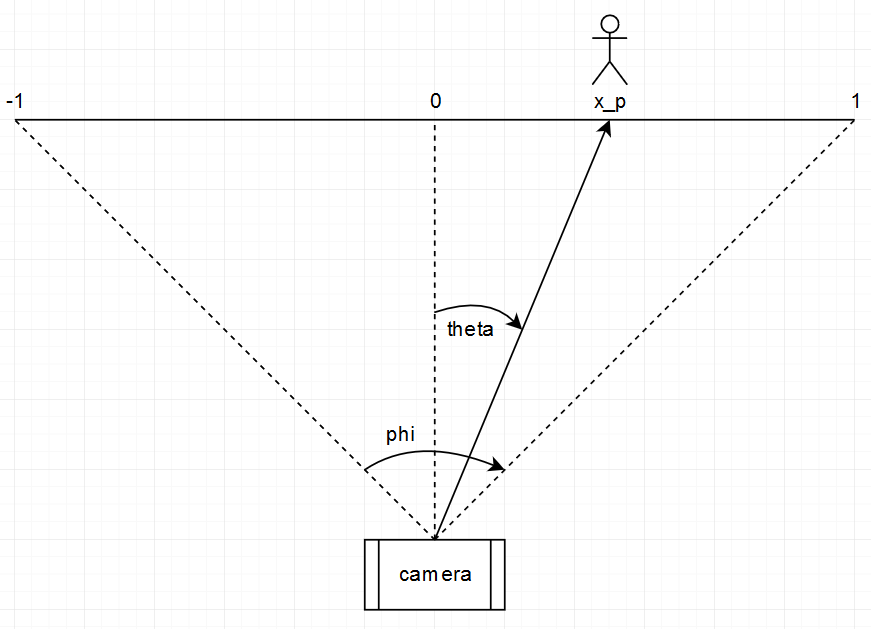
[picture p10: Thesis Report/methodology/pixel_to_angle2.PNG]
  
  \caption{\label{fig:pixel_to_angle} Diagram showing the mapping from normalized pixel to angle.}
\end{figure}

Note that the pixel coordinate of the detected object is given by \pyth{x_p} ($x_p$), the angle to the object is \pyth{theta} ($\theta$) and the field of view of the camera is \pyth{phi} ($\phi$). Letting the distance between the camera and the plane at the closest point be noted as $L$, one can convert between pixel and angle as follows:

\[ L = \frac{1}{\tan{\phi/2}} = \frac{x}{\tan{\theta}} \]
Resulting in,
\[ \phi = \tan^{-1}{\left( x\cdot{}\tan{ \phi/2 } \right) }
\qquad or
\qquad x = \frac{\tan{\theta}}{\tan{\phi/2}} \]
%\phi = \tan^{-1}{\left( \frac{\tan{ \theta/2 }}{x} \right) }

A plot of this function is shown in Figure~\ref{fig:pixel_to_angle_plot} for a $\phi$ value of 75\textdegree. Clearly, the mapping from pixel to angle is nonlinear.

\begin{figure}[h!]
  \centering
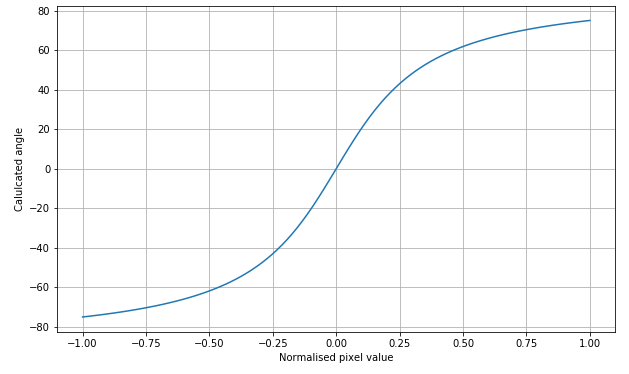
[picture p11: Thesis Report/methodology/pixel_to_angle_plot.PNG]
  
  \caption{\label{fig:pixel_to_angle_plot}Plot showing the mapping from normalized pixel to angle.}
\end{figure}

For this reason, an EKF was considered instead of a linear Kalman Filter - a one pixel error in the middle of the image will propagate to a different angular error than a one pixel error at the edge. The Jacobian could then be calculated as,

\[ \frac{\delta h}{\delta x} = \frac{\delta}{\delta x} \left[ \frac{\tan{\theta}}{\tan{\phi/2}} \right] = \frac{1 + \tan{(\theta)}^2}{\tan{\phi/2}} \]

For reasons explained in Section \ref{sec:kf_implementation}, both the KF and EKF were considered.

Next, the $Q$ and $R$ matrices needed to be determined. In most systems, these can be calculated after careful modelling of the objects dynamics and consultation with component datasheets. However, in this system, the $Q$ matrix determined for an object which is close to the camera would be wildly inaccurate when the object is farther away, since distance affects the perceived angular movement of an object moving in a straight line. Since there is no distance estimate, this could not be reliably factored into a constantly changing $Q$. In addition, the neural network has no obvious value to use for the sensor noise, $R$.

What is known, however, is how process uncertainty in the acceleration and velocity of the model would propagate to the the other states. Thus, the following structure was decided for the process uncertainty matrix $Q$:
\[ Q = \begin{bmatrix}
	Q_a \frac{\Delta t^2}{2} & 0 & 0 \\
	0 & Q_a \Delta t & 0 \\
	0 & 0 & Q_a \end{bmatrix} \]

Thus, $Q_a$ (the maximum amount of deviation from the acceleration model) and R were left as parameters to be tuned using recorded data.

\section{Implementation of the Kalman Filter algorithm}

While python wasn't designed for purely numerical programming (such as matrix multiplication), when the correct packages are used it can approach C-level speeds. \pyth{numpy} is one such package - it provides python bindings to C arrays, resulting in incredible speedups over regular python arrays.

For this reason, the Kalman Filter and Extended Kalman Filter were implemented as python classes which contain \pyth{numpy} matrices. The code can be found on the authors \href{https://github.com/alknemeyer/EEE4022S-Thesis-Project/blob/master/Final%20code/extended_kalman_filter.ipynb}{GitHub repository.}

\subsection{Timing issues due to sampling time inconsistencies}
Kalman Filters usually operate in control systems with constant loop times. However, due to the fact that the object detection pipeline had a variable amount of time between samples, the Kalman Filters time parameters (found in the $F$ and $Q$ matrices) needed to be continuously updated based on the actual amount of time that had passed since the last predict/update cycle.

This time stamp was also used to get a state estimate from the Kalman Filter between updates from the object detector.

Pseudo code which performs these operations is shown below.\\

\begin{python}
def update(measurement, previous_time):
	time = get_current_time()
	new_T = time - previous_time
	previous_time = time
	
	# update the time-dependant parameters
	new_F, new_Q = update_F_and_Q(new_T)
	
	predict(new_F, new_Q) # make predictions for x, P
	update(new_F, measurement) # compare to measurement

def estimate_current_position():
	time = get_current_time()
	temp_T = time - previous_time
	new_F, _ = update_F_and_Q(new_T)
	
	return new_F * x
\end{python}

\subsection{Tuning the process noise and sensor uncertainty}
The next step was to find and set reasonable values for the process noise $Q$ and sensor uncertainty $R$. Empirical data was gathered by running the computer vision algorithm while a human walked and ran around the lab. The results of this were saved to a file, allowing for easy offline simulation. A plot of the raw updates from the neural network are shown below, in Figure~\ref{fig:raw_nn_results}.

\begin{figure}[h!]
  \centering
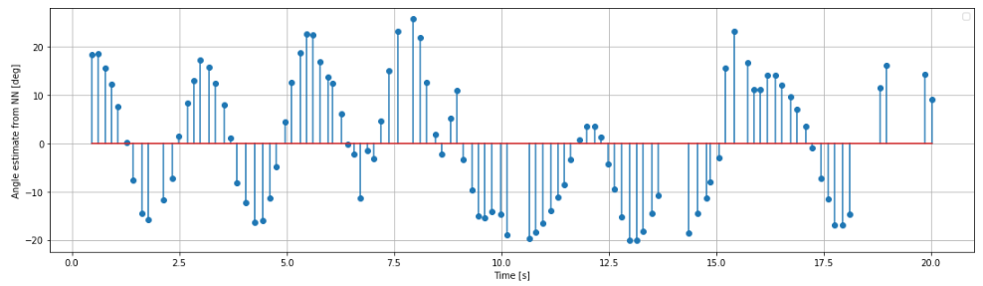
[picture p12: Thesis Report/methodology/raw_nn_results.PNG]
  
  \caption{\label{fig:raw_nn_results} A plot showing the output of the neural network (measured as a relative angle in degrees), and the timing thereof.}
\end{figure}

Note how the time between inferences from the neural network is not constant - while all of the calculations in the neural network are the same in each run, non-constant run times are the natural consequence of running a control loop on a non real time operating system.

In addition, there are times when a few hundred milliseconds pass without receiving a new update - this occurs when the neural network can't find an object in the frame. It is worth noting that the neural network is in fact very good at locating objects, and misses them infrequently. However, the frequent and large gaps in object locations was added in order to simulate tracking an object which may briefly disappear behind an obstacle (such as a bush) or not be found due to poor camera footage.

Next, a small script was made to speed up the trial-and-error process of comparing the advantages and disadvantages of a variety of $Q$ and $R$ values. The possibility of switching to a Kalman Filter and changing the acceleration modifying parameter $\beta$ were added. In the end, values were chosen to satisfy the following two criteria:

\begin{enumerate}
\item Trust the updates from the neural network more than the model itself. This was decided on because the network was known to accurately find objects in a frame, whereas the constant velocity or acceleration model was \emph{known} to be incorrect.
\item Make reasonable predictions in the event that no updates appeared from the neural network. 'Reasonable' meant that, if the data indicated that the object was moving in a certain direction at a certain velocity, it is reasonable that the object would keep moving in that direction and at that velocity.
\end{enumerate}

A plot of the interactive process and selected paramters is shown below, in Figure~\ref{fig:tuning_Q_R}.

\begin{figure}[h!]
  \centering
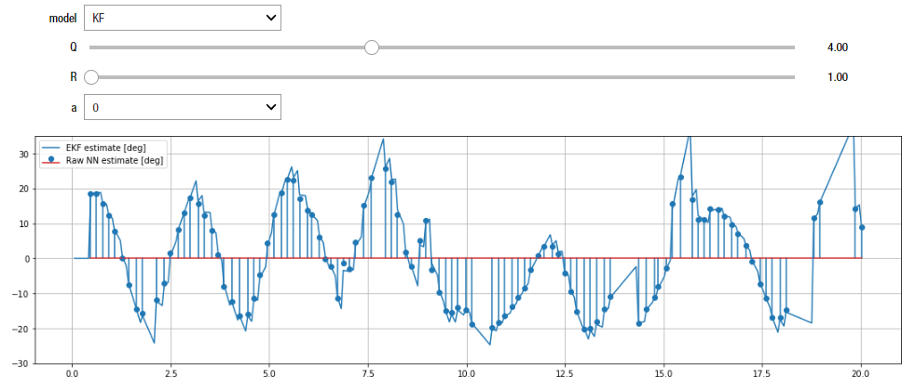
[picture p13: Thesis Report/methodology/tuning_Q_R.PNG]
  
  \caption{\label{fig:tuning_Q_R} A plot of the output of the EKF given stem plot data as input.}
\end{figure}

Following this process, choosing $Q = 4$, $R = 1$ and $\beta = 0$ ultimately resulted in an KF which closely follows and trusts the updates from the neural network, whilst making reasonable predictions in the event that no data was received. Choosing $\beta = 0$ changed the model from constant velocity to constant acceleration, which was useful to avoid quickly growing spikes.

It is worth noting that the input data was more sinusoidal than 'roughly constant velocity', which was the main assumption behind the dynamics of the model. This was due to a lack of running space in the mechatronics engineering lab - once wall has been reached, there's no place to go except backwards. Testing on data gathered in a different way would result in a different choice of parameters.

The KF tracking the pitch used $R=50$ as its sensor noise parameter. This is because wild fluctuations in the centroid of the bounding box occurred each time the object walked behind an object which concealed the bottom part of the objects body. Thus, setting a high $R$ smoothed out the otherwise jerky behaviour.

In addition, since $Q$ specifies process noise in the angular dynamics of the system, it should really be updated according to the distance to the tracked object as this affects the maximum expected angular velocity and acceleration. There were two reasons why this was not implemented:

First, there was a lack of spatially-varied data. Second, there is not robust way of estimating the distance to the object (short of a distance sensor). One thought was to use the bounding box as a proxy for this, though more thought to this indicated that it would not work. Using the height of the box would fail each time the object stood up or extended its legs, using the width would fail if the object extended its arms or body, and using the area would likely fail in both of these cases.

\subsection{Choosing Kalman Filter or Extended Kalman Filter}\label{sec:kf_implementation}
While an EKF would be a more natural fit for the system owing to its nonlinear sensor, it was found that the linear Kalman Filter was a good option if the nonlinearity was removed by converting the pixel coordinate to an angle before passing it to the neural network. The Jacobian wasn't correct, but the filter still functioned quite well.

This was done after numerous incorrect implementations of the EKF removed the authors trust in his programming skills. Since the KF was well understood while the EKF wasn't (at the time of the tests) the KF was used in the final system for risk mitigation reasons.

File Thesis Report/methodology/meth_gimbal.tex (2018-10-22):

\chapter{The Gimbal}
Once an object had been found and a desired control action calculated, the camera needed to be rotated so as to track it. This required the use of a camera gimbal which is powerful enough to rotate the payload specified by the researchers who will ultimately use the system: two GoPro Hero Session cameras, a distance sensor and the small camera used for tracking. Since no system was available which supports this payload, a new gimbal had to be designed and built.

\section{The gimbal frame}
There are already a number of gimbal systems available for purchase, and gimbal designs available for free use. However, the requirements of the gimbal narrowed down the options significantly. Gimbals typically need only keep a single small camera level, or rotate according to commands from an RC system. This project required a gimbal which has space for two cameras spaced a few centimetres apart and can rotate according to commands from a Raspberry Pi. This necessitated the design of a new system.

While they couldn't be used without modification, the designs mentioned subsection \ref{ssec:gimbal_design_inspirations} were a good enough reference point that a new system could be created with relative ease.

Some priorities for the new gimbal design were as follows:

\begin{itemize}
\item It should be possible make the frame using equipment available at the university, such as a laser cutter or 3D printer.
\item It should be straightforward for someone to modify the design to house a new gadget.
\item In order to minimize the strain on actuators and the control system, there should a mechanism to help balance the gimbal.
\item As a result of the cameras being placed a few centimetres, there is an unbalanced torque. The effects of this should be minimized.
\end{itemize}
%
Based on these criterion, a gimbal was designed using SolidWorks, a CAD software used frequently in engineering design. A render of the final model used for this project is shown in Figure~\ref{fig:assembled_render}.

\begin{figure}[h!]
  \centering
  %\includegraphics[width=\textwidth]{methodology/assembled_render}
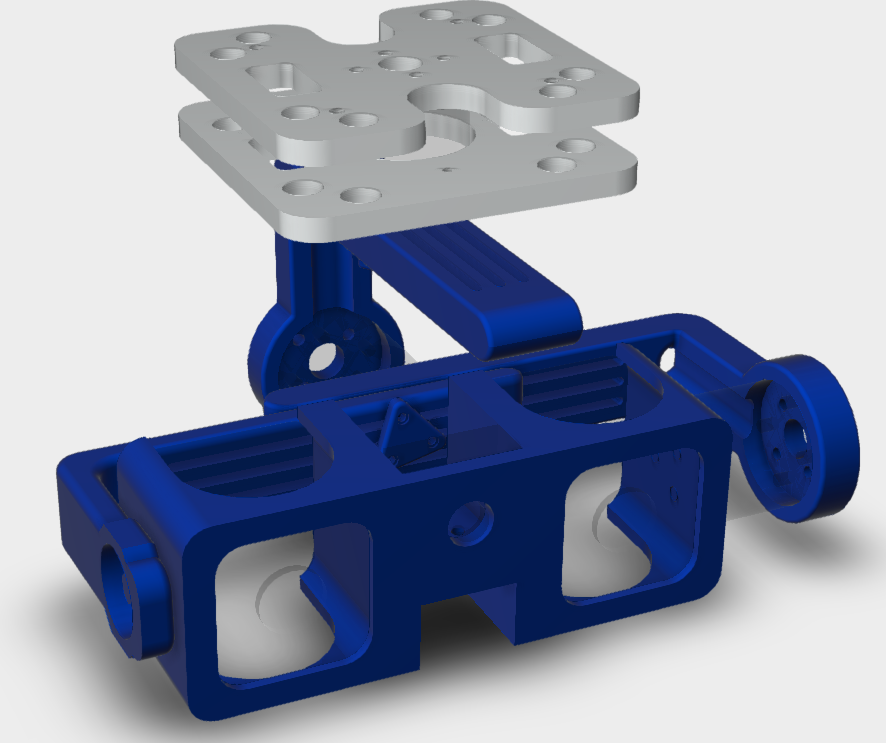
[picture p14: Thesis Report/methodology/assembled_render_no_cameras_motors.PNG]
  
  \caption{\label{fig:assembled_render} A render of the gimbal designed for this project.}
\end{figure}

The mounting panels on top were made by laser cutting hardboard, while the blue components were produced using a 3D printer.

Figure~\ref{fig:annotated_assembly_with_cams} shows the mount where the payload is placed. The GoPro's buttons can be easily reached, and there was space to place an IMU almost exactly in the center of rotation.

\begin{figure}[h!]
    \centering
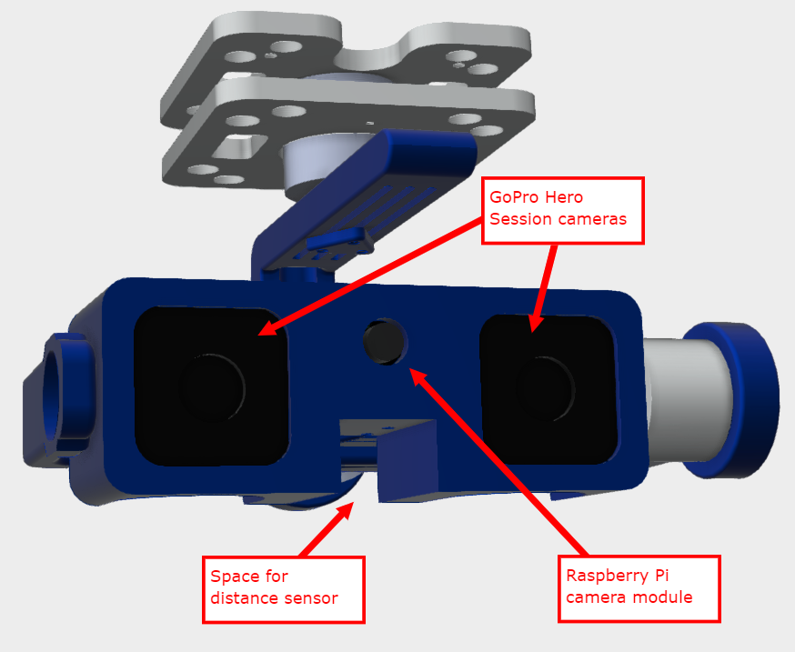
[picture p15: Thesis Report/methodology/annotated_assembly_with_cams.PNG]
    
    \caption{\label{fig:annotated_assembly_with_cams}An annotated render of the gimbal, showing where the cameras and distance sensor lie.}
\end{figure}

As can be seen in Figure~\ref{fig:annotated_assembly_no_cams}, the payload mount could be modified without needing to extend and reprint the mounting brackets. This also had the effect of making it easy to move the mass around to balance the gimbal. The addition of a support bracket mitigated the effect of a potentially large torque from the two cameras. Finally, the holes in the wooden plate on top were filled using vibration dampers.

\begin{figure}[h!]
    \centering
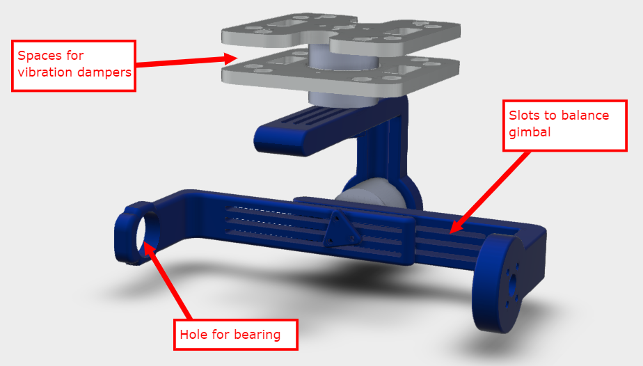
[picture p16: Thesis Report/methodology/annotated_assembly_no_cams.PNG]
    
    \caption{\label{fig:annotated_assembly_no_cams}An annotated render of the gimbal, showing the slots used to balance the gimbal, the hole for the bearing and spaces for vibration dampers.}
\end{figure}

A final useful feature was the ability to switch between 2- and 3-axis mode by removing the roll motor and top most L-bracket, and rotating the bottom portion of the frame by 90\textdegree.

\section{Assembling the gimbal}
After the frame had been 3D printed/laser cut, and the controller and motors purchased, the gimbal was ready for assembly.

It was decided that the 2-axis mode would be used for tests: this way, the gimbal would draw less power (due to using two motors instead of three) and there would be an extra motor available in case one broke. It also simplified the balancing process, as there was one less axis to worry about. A photo of the final built gimbal is shown in Figure~\ref{fig:photo_of_gimbal}.

\begin{figure}[h!]
    \centering
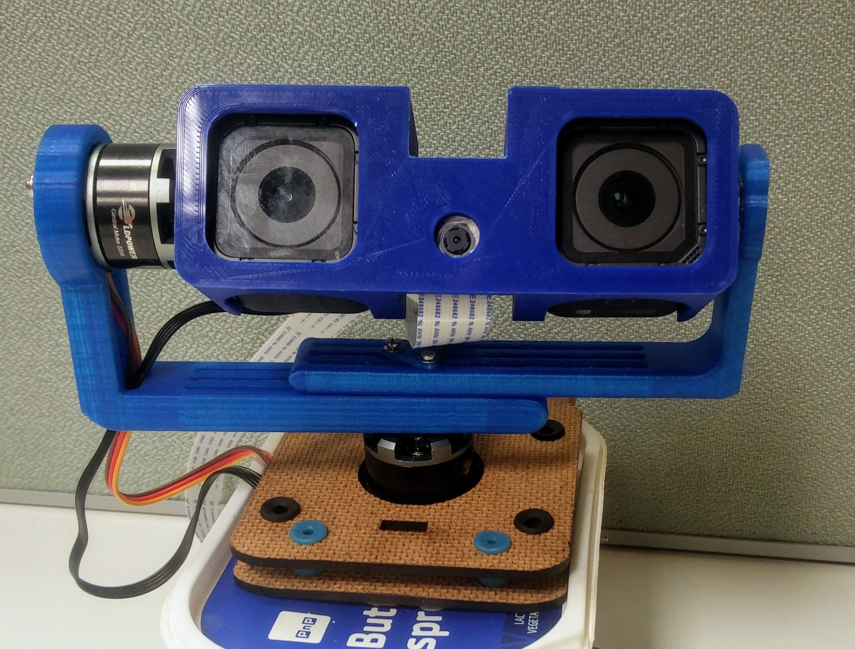
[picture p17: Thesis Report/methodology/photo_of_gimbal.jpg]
    
    \caption{\label{fig:photo_of_gimbal}A photo of the 3D printed and assembled gimbal.}
\end{figure}

Four LD-Power 2208 BLDC gimbal motors were used, based on the comparison in Subsection \label{ssec:gimbal_comparison} and because they were available second hand at a good price. Due to the small market for gimbals, they are simply rewound high-speed quadcopter/airplane motors, made to work at lower speeds with higher torque \cite{website:rewinding_bldc_gimbal}.

\section{The gimbal controller}
Properly controlling BLDC motors to stabilize a gimbal is an entire project on its own. Luckily, there are well-designed existing products which easily fulfil the requirements needed. While research was made into the strengths and weakness of the various options available, factors such as local availability, price and time until reception of the gimbal resulted in a single actual choice: purchasing a second hand BaseCam Electronics Simple Brushless Gimbal Controller (SBGC) 32-bit controller \cite{website:basecam_sbgc} from someone who used it for drone footage.

The controller is powered off a 8-25V source and has built in power electronics, simplifying the number of components required. Up to three BLDC gimbal motors can be powered off the device.

The angular state of the gimbal is estimated using an IMU placed near the camera. The IMU contains an accelerometer and a gyroscope.

\subsection{The Serial API}

It also has an entire serial API which allows an external computer to write commands to and read information from the gimbal. Example commands include setting motor angles and rotation rates, while those same variables can be read from the controllers built in Kalman Filter (which estimates those states).

The controllers serial API is specified in a 53 page document \cite{website:sbgc_serial_api}. The manufacturer also provides an Arduino implementation of the serial API. However, since the rest of the project was implemented in python, it was decided that the relevant communication protocol would be re-implemented in python. In addition, since a variety of users on the BaseCam forums have mentioned that they would appreciate having access to such a python module, the library will be released for free on the forums. It can be found on the authors \href{https://github.com/alknemeyer/EEE4022S-Thesis-Project/blob/master/Final%20code/gimbal_control.ipynb}{GitHub repository.}

The serial API was made to work by looking through the specification, reading the code in the Arduino implementation and finally visualising the serial output of the Raspberry Pi using an oscilloscope as a last resort debugging technique.

\subsection{Tuning the controller}
The gimbal controller offered an 'auto-PID' tuning algorithm, but for unknown reasons this didn't work very well. Thus, the controller was tuned manually by first adjusting the Proportional term until a fast response was achieved, then the Integrator term until the system began oscillating, and then finally the Derivative term until the overshoot stopped. Then, each term was tweaked until a smooth yet robust response was achieved.

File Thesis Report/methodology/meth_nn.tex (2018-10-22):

\chapter{Computer vision implementation}

Having performed a review of literature relevant to the project, it was time to actually build the tracking system.

This chapter describes the steps required to establish a complete computer-vision workflow. Unlike other chapters in this report, it is likely that the software presented here will quickly become outdated - multiple computer vision frameworks are competing for market attention, and changing a lot while doing so \cite{website:comparison_deep_learning_software}. In addition, neural accelerator technology is in its infancy and likely to improve a lot in the coming years. Thus, the section is presented as a general methodology which tries to be independent of framework and branding where possible.

Following this, the actual implementation of the computer vision system is discussed along with some short tests on its performance.

%It should be noted that a lot of mistakes were made in this part of the project - these won't be discussed.

\section{Workstation setup and testing}
Three independent computers were used as part of the complete computer vision workflow - a mid-range GPU-equipped computer to prototype and train neural networks, a regular laptop to test and compile a trained neural network and an small embedded computer which uses the neural accelerator for inferencing.

One software package common among all three computer was git \cite{git}, which was used extensively to keep the files on all three computers synchronized.

\subsection{Setting up a computer for training}
Depending on the selection of computer vision/deep learning framework and the operating system on which it is installed, setting up a computer to train neural networks can range from trivial to extremely difficult. However, there are some commonalities amongst the popular frameworks.

The first step is usually to install CUDA, a GPU-acceleration software developed by NVIDIA for their GPUs \cite{nvidia_cuda}. At the time of writing, most frameworks simply don't support AMD GPUs. Next, install cuDNN, NVIDIA software specifically aimed at increasing performance for deep neural networks \cite{nvidia_cudnn} on their GPUs.

If needed for the deep learning framework, install an appropriate version of python \cite{python}.

Finally, the framework itself should be installed. In this project, three frameworks were tested on Windows.

The first two were TensorFlow and Keras. These are installed using pip, pythons built in package manager. The installation is done by entering the command,\\
\pyth{python -m pip install keras tensorflow-gpu}.

The last package was Caffe. Installation on Windows is difficult due to a lack of support for the OS, and wasn't accomplished during the course of the project.

It should be noted that, if the network will simply be fine-tuned (ie, the network was already trained on a similar dataset and requires minimal further training) then one might actually get away with training the model on a fast CPU.

\subsection{Setting up a computer for testing and compiling}
Most simple tests were run on an easily accessible computer. If using the Movidius NCS, this computer must run a Ubuntu 16.04 as it is the only non-Raspbian desktop OS the Movidius SDK officially supports \cite{website:movidius_install}. Movidius software barely works as is, so it is not recommended to push things even further by messing around with any other OS.

One option is to run Ubuntu on a virtual machine, such as Oracle VirtualBox. If you do this, don't bother trying to make it work with the NCS hardware through the VM - it can be quite tricky getting the drivers to work. Instead, trust that the compiled network will perform as well on the NCS as it does in the uncompiled framework-specific format and save yourself a lot of time.

Next, install the Movidus SDK, as described in the documentation \cite{website:movidius_install}. Despite what the documentation suggests, there isn't a need to \pyth{make} all the examples - this can take a couple hours, use a lot of disk space and not help at all.

After this, the previously trained neural network should be compiled to the Movidius-specific graph format using the \pyth{mvNCCompile} command. If it fails, it is likely that the network has an operation which isn't supported by the Movidius software. To this end it is highly recommended to check whether the operations used in the neural network are supported by Movidius for that particular frame.

If the Movidius SDK installation process has not already done so, it is recommended to install the deep learning framework that will be used. This enables the user to debug their neural network without having access to the inference computer.

\subsection{Setting up a computer for inferencing}
A Raspberry Pi was chosen as the embedded computer that would interface with the neural accelerator. An SSH terminal was used to access it. In order to get it ready for the final platform, some packages needed to be installed - a list of the most relevant python packages not included in a default python installation is as follows:

\begin{itemize}
	\item \pyth{numpy}: a package for fast numerical computing.
	\item \pyth{picamera}: a package to facilitate the use of the Pi Camera module.
	\item \pyth{matplotlib}: a popular plotting library.
	\item \pyth{PIL}: an fast library useful for working with images.
\end{itemize}

These are easily installed by entering the following command in a terminal:\\
\pyth{python -m pip install numpy picamera matplotlib PIL}

Interestingly, it is not actually necessary to install any deep learning framework on the Raspberry Pi. Neither is it necessary to install \pyth{opencv} or even the full Movidius SDK if the neural network has already been compiled to a graph file. Knowing this can save you an absolutely incredible amount of time, as these programs can be incredibly time consuming and frustrating to install. For instance, installing the full Movidius SDK on the Raspberry Pi requires upwards of 10 hours and is prone to failing at almost any point in this installation.

Thus, it is \emph{highly} recommended to instead skip all of these potential issues and rather just install the Movidius SDK in API-only mode \cite{movidius_api_only}. This doesn't take long and is not prone to failure.

Python notebooks were used for all actual programming. In this project, the main advantage to using notebooks was the fact that the notebook server could be port-forwarded to the main development PC, allowing for far easier plotting and visualisation than would be possible using a simpler IDE in an SSH terminal. Note that was important that the code ran on the Raspberry Pi itself to access its hardware, and connect the Pi to an external display would not be ideal as its GPU was needed for other computation.

\section{Selection of computer vision framework}
At the time of writing, the Movidius NCS only supports the TensorFlow and Caffe machine learning frameworks \cite{website:movidius_install}. Based largely on its popularity and ease of use, TensorFlow was chosen as the architecture which would be used for the project \cite{website:tensorflow_popularity}. However, TensorFlow is quite low-level and provides fairly slow and inconvenient methods of model creation, training and testing. It certainly has advantages but ease of development is not one of them.

To combat this, another option is to instead use Keras, a deep learning library which provides a far more intuitive interface. It allows the user to specify which backend they'd like to use for the actual number crunching. Among other options, one of the available backends is TensorFlow. The popularity of Keras has grown to such an extent TensorFlow has incorporated it as an official API.

The plan was then to retrain a neural network (possibly after modifying it) using Keras, export the model architecture and weights in TensorFlow format, and then compile it down to the Movidius NCS graph format. The hypothesis was that while researchers often aim to create neural networks which can classify more and more types of classes at once, this project only required up to three: cheetahs, humans and dogs. This meant that useless parts of the network (neurons which never fire as they aren't needed) could potentially be removed \cite{molchanov2016pruning}. This process is known as 'pruning', and can significantly decrease inference time.

However, after far, far too much frustration, it was discovered that the support for each framework was far from equal. Networks created in TensorFlow quite consistently failed to compile. After examining the Movidius documentation more closely, it was discovered that the number of operations supported for TensorFlow was simply far smaller than the number supported for Caffe. For instance, the TensorFlow \pyth{concat} operation doesn't appear on the list of compilable operations. This left Caffe as the only other available framework.

\section{Selection of CNN architecture}
By this stage, the work spent on object detection had exceeded time estimates and was threatening to compromise the time available for the other components in the system. In addition, Caffe has extremely poor support for Windows machines and no there were no dedicated GPU-enabled Linux PC was available for use as a neural network training machine. For these reasons, it was decided the an unmodified pretrained Caffe model would be used.

%https://github.com/movidius/ncappzoo/tree/master/caffe
In order to mitigate further risk of a model not working correctly on the NCS, only architectures with official support from Movidius were considered. At the time, this narrowed the choice down to a single option: SSD MobileNet, the combination of MobileNet and SSD, two independently designed neural network architectures.

MobileNet is a class of image classifiers designed by researchers at Google \cite{arXiv:1704.04861}. Since it was designed for mobile devices, it trades some classification accuracy for performance. However, the architecture is remarkable in that the performance increase is usually significant while the classification accuracy decrease is not. It acts a feature extractor in this particular model.

SSD (short for Single Shot MultiBox Detector) is a an object detector \cite{arXiv:1512.02325}. When used with another network as a feature detector, it takes in features, scales them to a variety of sizes and finally, after some more processing, outputs a vector which embeds information on the number of objects found, the predicted class for each object, pixel coordinates of the bounding box around each object and a number from 0 to 1 which represents the confidence in the network's prediction. Hence, the name - a single pass through the network resulting in the detection and boxes of multiple objects.

As a backup, another option would have been to perform the sliding window technique using an image classifier. There could be merit to this: a clever algorithm might first search parts of the image where it expects to find the object, reducing the overall computational requirements.

\section{Implementation of computer vision system}
Once all required software packages were installed, the next step was to start integrating the various components in the computer vision pipeline.

\subsection{The Raspberry Pi camera}
For the sake of convenience and low latency imaging, it was decided that a Raspberry Pi v2 camera module would be used to provide a stream of photos for the CNN. The camera plugs into a Raspberry Pi using a flat ribbon cable, as shown in Figure~\ref{fig:r_pi_camera}.

\begin{figure}[h!]
  \centering
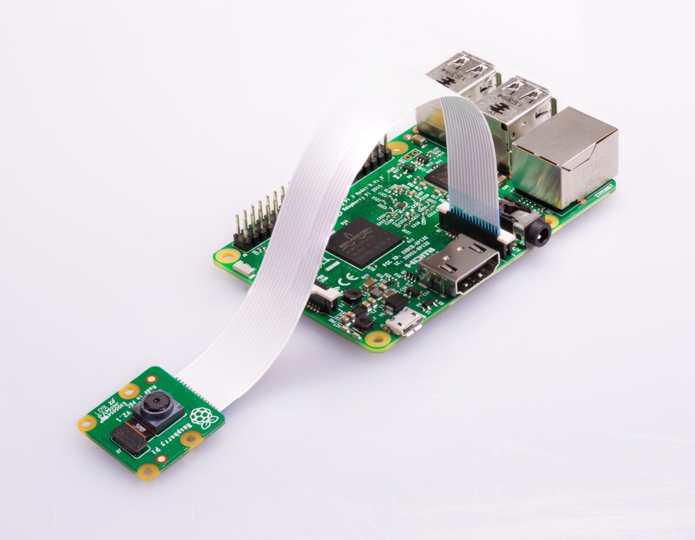
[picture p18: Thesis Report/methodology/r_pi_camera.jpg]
  
  \caption{\label{fig:r_pi_camera}A photo of a Raspberry Pi connect to a Raspberry Pi camera module.}
\end{figure}

An alternative would be to attempt to stream from the GoPro cameras themselves, but this would result in a higher latency as the photos have to be transferred via WiFi and would not use the Pi's built in hardware encoding \cite{website:gopro_to_rpi, website:gopro_to_rpi2}.

As described in the excellent \pyth{picamera} module documentation \cite{website:picamera_hardware}, one must be careful about selecting a sensor mode and camera resolution which makes use of the full FOV available (62.2\textdegree $\ \times$ 48.8\textdegree). Lower resolutions and fast sensor modes tend to take a simple crop of the centre of the image (reducing the FOV) instead of taking a full photo and resizing it. The price paid for this is latency - the higher the resolution, the more data flows through the pipeline and computation must be done.

A resolution of \pyth{1640 x 1232} maximised the FOV. Since the Pi Cameras sensor resolution is \pyth{3280 x 2464}, it uses 2$\times$2 binning to easily achieve this downscaling. Next, the Pis GPU was used to easily resize the image down to \pyth{320 x 304} - only a few resolutions are support by the library and this one was close to the resolution typically used by CNNs, so further resizing on the Pis CPU would require minimal processing time.

Finally, the video port was used to take photos instead of the camera. This was done to decrease latency - while both the video port and still port constantly send photos down the ribbon cable to the pi, using the video port results in less anti-noise post-processing (and thus lower latency).

%As is normal in Python, once the exact problem had been understood, the solution in code was relatively straightforward. The following code is enough to set up the pipeline mentioned thus far: \\ \\ \\ \\

%\begin{python}
%with picamera.PiCamera(resolution=(1640, 1232),
%                       framerate=40,
%                       sensor_mode=5) as camera:
%     # (320, 304) is closest to neural network input of (300,300)
%    frame = picamera.array.PiRGBArray(camera,
%                                      size=(320, 304))
%    # use GPU for resizing - will resize to nn_shape later
%    cont_capture = camera.capture_continuous(frame, 'rgb',
%                                             resize=(320, 304),
%                                             use_video_port=True)
%\end{python}

%After this, a simple function call of \pyth{next(cont_capture)} would fetch the latest frame from the continuous stream of photos, perform some post-processing and then place it in the \pyth{frame} buffer, where it could be accessed using \pyth{frame.array}.

\subsection{Compiling a trained neural network}
A trained SSD MobileNet was found on GitHub user chuanqi305's \href{https://github.com/chuanqi305/MobileNet-SSD}{online git repository} \cite{website:chuanqi305_nn_github}. It has an input dimension of $300 \times 300 \times 3$, and was largely trained on MS-COCO before being fine-tuned on VOC0712 (MS-COCO and VOC0712 are two large, freely available datasets \cite{website:mscoco_dataset, website:voc2012_dataset}). It was trained to predict make predictions for 20 classes, including 'person', 'dog' and 'cat'. The reason for choosing a network which predicted these classes, was because tests would be done on (easily accessible) humans and dogs. In addition, if the network was to be retrained to detect cheetahs, starting from detecting cats or dogs might help decrease training time and the amount of data required.

After confirming that the license for usage of the model is permissive, it was downloaded and then compiled on a windows laptop running an Ubuntu VM with the full Movidius SDK installed, using the \pyth{mvNCCompile} command. The graph file was then transferred to the Raspberry Pi via an ssh terminal.

Using Movidius code from tutorials as a starting point, the graph file was uploaded to the NCS. The camera module presented above was then used to take a photo and store it as an array of unsigned 8-bit integers (integers from 0 to 255).

The CNN used required some preprocessing before an image could be passed in as an input. Specifically, the images should be represented as an array of floats with a mean of 0 and a range of $(-1, +1)$. This was done using the calculation,%\\ \\

\begin{python}
mean = (127.5, 127.5, 127.5)  # 3 colour channels, 255/2 == 127.5
scale = 1/127.5
preprocessed_img = (img - np.float32(mean)) * np.float32(scale)
\end{python}

Pre-processed images were then sent to the NCS, which passed them through the CNN in a time of about 80 ms. The serialized output of SSD network was then decoded into a python dictionary which contained easy to manage information about the objects in the frame.

\section{Testing the computer vision model}
The next step was to test the data pipeline created thus far. The main issues being tested were,

\begin{enumerate}
\item The general classification accuracy of of the network,
\item The extent to which the predicted position overlaps with the actual position,
\item How blurry/dark/out of focus the image can be before the network stops working, and finally,
\item The inference time of the network, with and without the NCS.
\end{enumerate}

Code to redo these tests can be found on the authors \href{https://github.com/alknemeyer/EEE4022S-Thesis-Project/blob/master/Final%20code/tests.ipynb}{GitHub repository}.

\subsection{Accuracy of the predictions}

The setup was tested by passing photos through the neural network, and then superimposing the predicted bounding box output onto the image along with a text description of the predicted class. A measure of confidence (written as a percentage by convention, but not actually a statistical measure) was also added to show how trustworthy the prediction was.

First, a photo of the author's dog was tested. The network correctly predicted 'dog' with a high confidence measure of 99\%. This is shown in Figure~\ref{fig:box_around_blossom}.

\begin{figure}[h!]
  \centering
  
  \caption{\label{fig:box_around_blossom}A photo of the authors dog, correctly predicted with 99\% confidence.}
\end{figure}

Next, three images of the author were tested. They are shown in Figures~\ref{fig:box_around_me_crouching}, \ref{fig:box_around_me_running} and Figure~\ref{fig:box_around_people_hard}.

\begin{figure}[h!]
    \centering
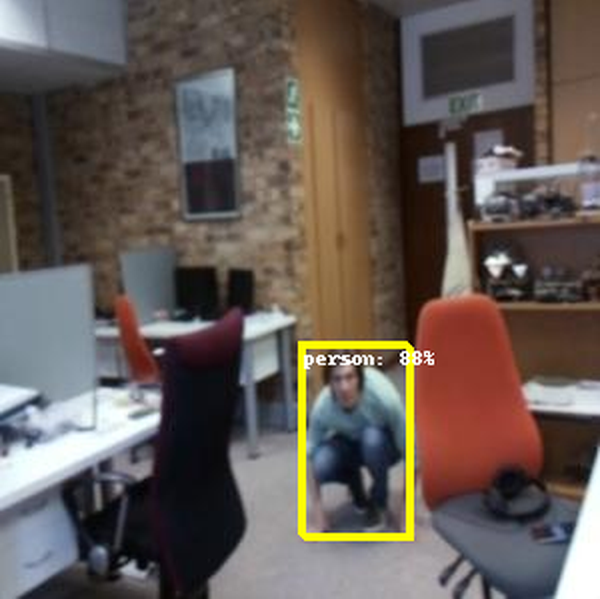
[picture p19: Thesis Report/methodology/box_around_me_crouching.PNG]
    \subfloat[][A photo of the author while crouching, correctly predicted with 88\% confidence.]{\label{fig:box_around_me_crouching}}
	\quad
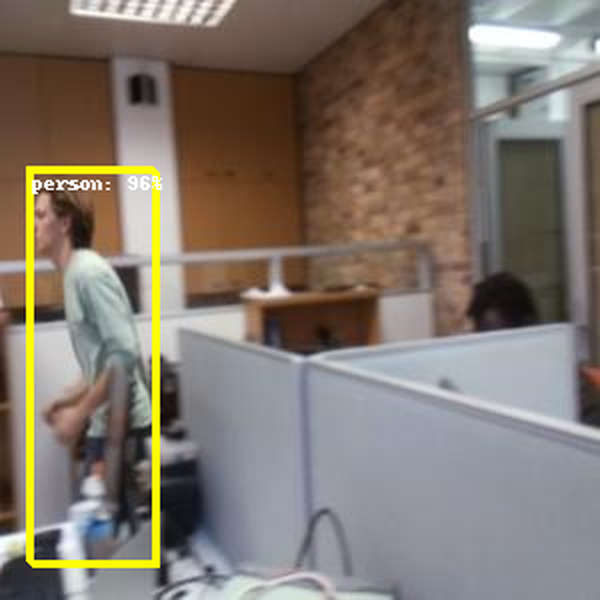
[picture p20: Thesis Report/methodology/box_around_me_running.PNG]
    \subfloat[][A photo of the author while running, correctly predicted with 96\% confidence.]{\label{fig:box_around_me_running}}
    \caption{Photos of the author looking silly while moving around a laboratory.}
\end{figure}

Figures~\ref{fig:box_around_me_crouching} and \ref{fig:box_around_me_running} show that the neural network can correctly classify objects in non-standard positions (such as when the classified object is in a crouch position, or from the side) in relatively complex environments, such as a laboratory with textured brick walls. The camera was moved slightly during both of the photos, resulting in slightly blurred images. This was done to emulate the gimbal moving the camera system. The confidence ratings were 88\% and 96\% respectively.

The final image, shown in Figure~\ref{fig:box_around_people_hard}, was a bit of a surprise in that the network far surpassed the authors expectations.

\begin{figure}[h!]
  \centering
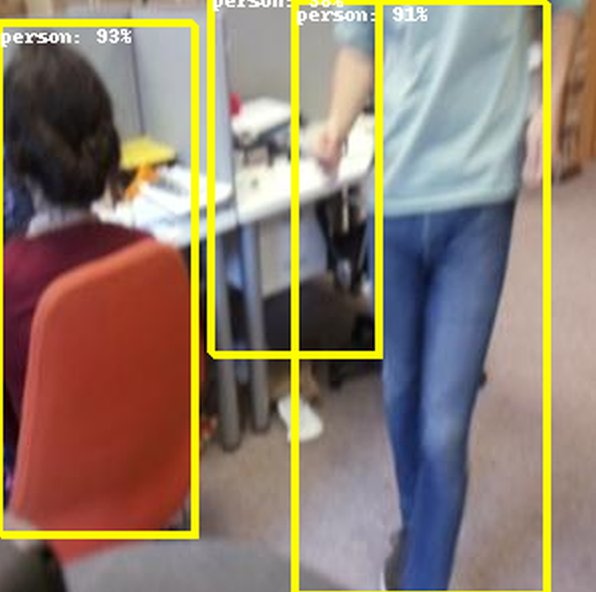
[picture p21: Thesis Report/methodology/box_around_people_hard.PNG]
  
  \caption{{\label{fig:box_around_people_hard}A photo of a person sitting and the bottom two thirds of another person standing, correctly predicted with 93\% and 91\% confidence respectively.}}
\end{figure}

Two people were correctly identified: a woman at a desk in the left of the frame with a confidence of 93\%, and the bottom two thirds of the author on the right side with a confidence of 91\%. Faces have been one of the easiest things to detect in computer vision \cite{website:face_detection_survey}, so it was a pleasant surprise to find that the network doesn't need a face at all.

There was also a false-positive detection in the centre of the frame. However, the confidence for this detection was 38\% - low enough that the recommended confidence threshold of 70\% confidence \cite{website:chuanqi305_nn_github} would have resulted in it being ignored.% \\

\subsection{Observed performance increase due to NCS}\label{ssec:meth_nn_performance_increase}
Next, the performance increase of the NCS was tested to confirm that the device was in fact necessary. For the purposes of the tests, the pre-processing time and latency of the camera were ignored as they are common to all methods of inferencing. It is worth noting that there will always be variability when timing the runtime of a process on a non-realtime OS using a language which occasionally pauses for garbage collection.

First, the Pi was tested on its own. Using the CPU, roughly a full second was required to get from pre-processed image to serialized results. Due to multithreading, up to four images may be processed side by side (staggered 250ms apart) for a total sampling rate of 4 Hz with a latency of 1 second.

Next, the Pi was tested with the Movidius NCS. It took around 20 ms to send the image to the devices memory, and then around 80ms to receive the result. The NCS can't process multiple images simultaneously, so this equated to a speed of 10 Hz with a latency of 100ms.

This proved that, short of using another form of CNN acceleration, the NCS was vital to the project's success.

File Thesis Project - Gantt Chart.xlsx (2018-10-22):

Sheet: Sheet1
THESIS PROJECT PLAN | 2018-06-25 |  |  |  |  | 2018-07-02 |  |  |  |  | 2018-07-09 |  |  |  |  | 2018-07-16 |  |  |  |  | 2018-07-23 |  |  |  |  |  |  | 2018-07-30 |  |  |  |  |  |  | 2018-08-06 |  |  |  |  |  |  | 2018-08-13 |  |  |  |  | 2018-08-20 |  |  |  |  | 2018-08-27 |  |  |  |  | 2018-09-03
 | M | T | W | T | F | M | T | W | T | F | M | T | W | T | F | M | T | W | T | F | M | T | W | T | F | S | S | M | T | W | T | F | S | S | M | T | W | T | F | S | S | M | T | W | T | F | M | T | W | T | F | M | T | W | T | F | M | T | W
Planning + revision: of project + previous work
Educate: watch fast.ai part 2, read papers and blogs
Set up pi: everything got mangled -> reinstall
Hardware test: compile NN into graph, put on NCS
Set up minibeast: install python, tensorflow, etc
Data: collect + label data of humans, preprocessing
Create NN: recognise an obj + find it in the frame
Compile a NN: switch to tf, finetune model, compile
Test the NCS: stick + NN + camera all works live
Camera gimbal: compare options, order
Camera gimbal 2: fetch, print frame, assemble, test
Extended Kalman Filter: understand + implement
Rpi to gimbal comms: create and test serialAPI
Integration time: put everything together, test
Convert to cheetah tracker: data, train
Do tests: in lab, put on quad, animals, etc
Write up thesis: lit. review, make backups, LaTeX
Poster + presentation: sleep --> prepare
Misc to do

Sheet: Sheet1 (old)
THESIS PROJECT PLAN | 2018-08-20 |  |  |  |  | 2018-08-27 |  |  |  |  | 2018-09-03
 | M | T | W | T | F | M | T | W | T | F | M | T | W
Camera gimbal: design, 3D print, put together
Extended Kalman Filter: understand + implement
Work on control: make it track pan + tilt
Buffer: just in case things take long
Convert to cheetah tracker: data, train
Work on "extras": eg put on quad, etc
Write up thesis: lit. review, make backups, LaTeX
Poster + presentation: sleep --> prepare
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

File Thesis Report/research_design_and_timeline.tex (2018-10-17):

\chapter{Research Design and Timeline}

{\Large \color{red} integrate some of these points into other areas, then just delete the chapter}

\section{Research Problem}
narrow angle gopro with computer vision better than multiple wide angled gopros??

\section{Elaboration of the Plan of Action}
Do the minimum complete system first, then work on any extras, even if they're core to the idea of the project

\section{Description of activies, methods and software platforms}
python for pretty much all software \\
caffe as DL frameworks \\
git to synchronize work done on pi, my laptop, VM and minibeast \\
extensive use of linux for development

\section{... validation}

\section{Project Timeline}
January/February: some intro to computer vision stuff. Preliminary research into NCS + initial setup on pi

June/July vac: (forgot exactly)

August/September: work on project

October: final tests, write up thesis, hand in. Also do poster and presentation

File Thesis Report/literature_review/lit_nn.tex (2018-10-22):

\section{Computer vision using neural networks}

Computer vision is an extremely large field of study on its own, but only a part of the system being designed. Thus, this section serves more as a light introduction to concepts and intuitions relevant to the project.

\subsection{Basic computer vision concepts}
While photo-based computer vision is a broad field, traditional techniques tend to be able to differentiate between classes of objects by using a number of cascaded filters, with each layer of filters being able to detect more and more complex shapes in an image \cite{website:cs231n_CNNs}. These filters are known as 'kernels', and are implemented as square (or cube) matrices which are convolved with the input image, a 2D (or 3D, for colour) array of pixel values.

As an example, Figure~\ref{fig:input_output_simple_filter} shows a simple image before (left) and after (right) being convolved with a vertical line finding kernel. Code to create this plot can be found in the authors \href{https://github.com/alknemeyer/EEE4022S-Thesis-Project/blob/master/Final%20code/Illustrations%20for%20report.ipynb}{GitHub repository}.

\begin{figure}[h!]%
    \centering
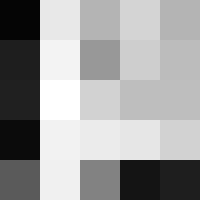
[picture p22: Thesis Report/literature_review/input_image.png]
    \subfloat[][Input image]{}%
    \qquad \qquad
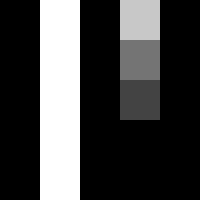
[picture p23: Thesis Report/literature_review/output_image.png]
    \subfloat[][Output Image]{}%
    \caption{An image, before and after being convolved with a vertical line finder.}%
    \label{fig:input_output_simple_filter}%
\end{figure}

Note how the the vertical line in the left part of the input has been found (represented by bright pixels in the output image). The horizontal line on the bottom right has been rejected. The faint vertical line in the top right has been found, albeit faintly.

The exact same transformation is shown in Figure~\ref{fig:simple_conv_as_numbers}, where the images have been replaced with their underlying matrices. The leftmost matrix is the pixel values of the input matrix, the middle is the kernel and the rightmost matrix is the output. \\ \\

%\begin{table}[h!]
%	\centering
%	\begin{tabular}{ p{0.5cm} p{0.5cm} p{0.5cm} p{0.5cm} p{0.5cm} p{0.5cm} p{0.5cm} p{0.5cm} p{0.5cm} p{0.5cm} p{0.5cm} p{0.5cm} p{0.5cm} p{0.5cm} p{0.5cm}}
% 5 & 232 & 180 & 212 & 180 &           &    &   &    &   & 0 & 255 & 0 & 200 & 0 \\
%30 & 243 & 152 & 206 & 188 &           & -1 & 2 & -1 &   & 0 & 255 & 0 & 116 & 0 \\
%32 & 255 & 210 & 190 & 190 & $\otimes$ & -1 & 2 & -1 & = & 0 & 255 & 67 & 0  & 0 \\
%11 & 242 & 235 & 230 & 210 &           & -1 & 2 & -1 &   & 0 & 255 & 0 &  0  & 0 \\
%90 & 240 & 130 &  20 &  30 &           &    &   &    &   & 0 & 255 & 0 &  0  & 0
%	\end{tabular}
%\end{table}

\begin{figure}[h!]
  \centering
  
  \caption{\label{fig:simple_conv_as_numbers}A simple image being convolved with a kernel, shown as matrices.}
\end{figure}

A larger, more interesting input image is shown in Figure~\ref{fig:image_kernel_demo} below.

\begin{figure}[h!]
  \centering
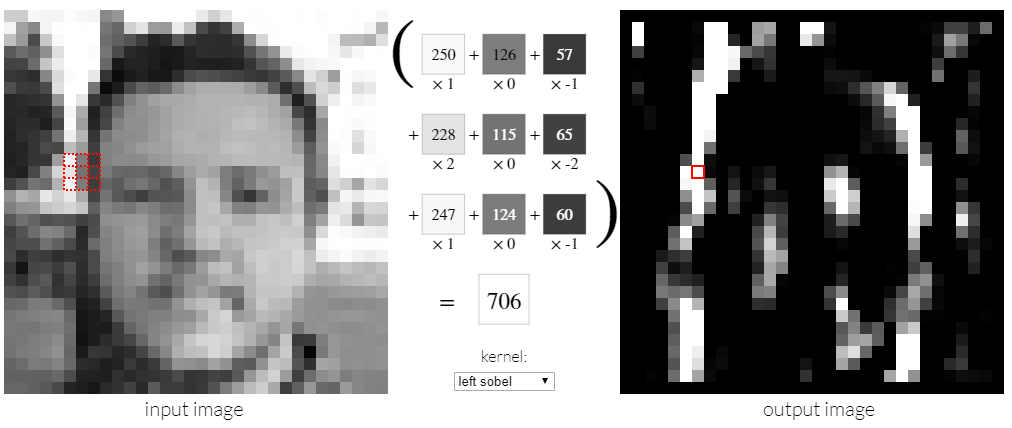
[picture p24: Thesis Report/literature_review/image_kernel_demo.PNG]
  
  \caption{\label{fig:image_kernel_demo}A demonstration of image convolution on a photo of a human \cite{website:setosa_kernel}.}
\end{figure}

The output image on the right hand side is the result of applying an edge-emphasizing filter. Note how the vertical lines around the shape of the face and nose are highlighted.

As an example of a complete system, consider a network of filters in which the first layer of kernels may detect vertical lines, angled lines, dots, and so on. These detections are then used as input matrices to the next layer, which will convolve them with a set of kernels to produce more complex detections. For example, two horizontal lines and two vertical lines may indicate the presence of a square in an image. A different configuration of lines may indicate a circle, and so on.

Carefully designing and combining these filters can ultimately result in the detection of an object. However, doing this by hand would be incredibly time consuming, and require extensive domain-specific knowledge in the field of computer vision to track a specific object. Even after the work has been put in to locate one type of object in a frame, locating another type of object could require the user to start from scratch.

\subsection{A brief introduction to machine learning}
Hand selecting kernels may work for simple problems, but for more complex applications, automating the selection of these values may become necessary. Machine learning algorithms (in which computers use datasets data 'learn' the parameters of a model) present a set of potential solutions to this problem \cite{website:cs231n_CNNs}. For computer vision, this boils down to using known input-output pairs of images of objects and labels corresponding to the classes of objects in each image to optimize the kernel values in the network of filters.

%TODO: {\color{red} talk a bit about neural networks (mainly fully connected layer type stuff) and include an image. mention the multi-layer perceptron. This part needs some work}

The standard method of doing this for images is through the use of Convolutional Neural Networks (CNNs), a class of large artificial neural networks \cite{website:cs231n_CNNs}. They typically consist of layers of kernels (as discussed previously) along with an array of other operations borrowed from the fields of computer vision and machine learning.

CNNs are initialized with random values in their kernels and random values for the transformations which combine the outputs of their kernels - only their general architecture tends to be fixed by human practitioners \cite{website:cs231n_CNNs}. These values are known as 'weights'. A summary of the method to get an optimal set of weights is as follows \cite{werbos1974beyond}:
%These values are known in the field as 'weights', while calculations are performed by 'neurons' - nodes in the CNN which perform an operation.

\begin{enumerate}
\item Initialize the CNN with a set structure and random weights.
\item Pass an image through the CNN, and take note of the output.
\item Get the error (the difference between the CNN output and the correct answer) and propagate it back through the CNN (known as 'backward propagation', or 'backpropagation'), adjusting the weights \emph{slightly} in such a way that that same input would be more likely to produce the correct output if run again (this is known as 'gradient descent', as it makes use of the partial derivative of each neurons computation to calculate how the weights should be adjusted).
\item Repeat the first three steps a few hundred or thousand times until the performance stops increasing. It is helpful to use a large dataset consisting of a diverse set of images.
\end{enumerate}

This process is known as 'training'. An illustration of the backwards propagation is shown in Figure~\ref{fig:backprop_nn}.

\begin{figure}[h!]
  \centering
  
  \caption{\label{fig:backprop_nn}An illustration showing inference (forward propagation) and error minimization (backward propagation) in a neural network \cite{website:backprop_img}. Each circle represents a computation (or neuron).}
\end{figure}

While it is possible that the CNN will act as an inefficient look-up table (mapping those specific inputs to their correct outputs, but giving the wrong result for a new image which it hasn't been exposed to \cite{werbos1974beyond} it is hoped that the CNN will instead map any \emph{similar} input to the correct output. As an example, a correctly trained CNN will map any image which \emph{looks} like a cheetah (has the correct body structure, spots, ear location, etc) to an output which is numerically encoded to represent "cheetah", even if it hasn't seen that particular image before. The process of taking an input and producing an output is known as 'inference'.

It should be noted that CNNs are nothing more than a nonlinear mapping from a vector of input pixels (the image) to a vector which represents certain outputs (where, for example, the first element in the vector represents "cheetah" as 1, "no cheetah" as 0, or even the coordinates of a cheetah. The second element could represent "hotdog" or "no hotdog", and so on. This is known as 'one hot encoding' \cite{website:one_hot_encoding}). Thus, in essence, this entire process is the solution to an optimisation problem: how to find the best set of weights to correctly map an input to the correct output.

\begin{figure}[h!]
  \centering
  
  \caption{\label{fig:one_hot_encoding}An illustration of one hot encoding. In this example, a value near one in the first index of the vector indicates a high likelihood of the image containing a cheetah.}
\end{figure}

%\begin{figure}[h!]
%  \centering
%  \includegraphics[width=0.8\textwidth]{literature_review/img_to_result}
%  \caption{\label{fig:img_to_result}A highly abstracted view of a CNN.}
%\end{figure}

CNNs simply require a few hundred or thousand labelled images and a few hours on a modern GPU, depending on the hardware and datasets available \cite{website:fastai_train_times}. There are many tips, tricks and open datasets which can be used to make this work easier.

\subsection{Key machine learning concepts and definitions}
Before getting lost in activation functions, dropout and the rest of the endless list of ideas in machine learning, it is worth considering the separation of jobs in modern data science.
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

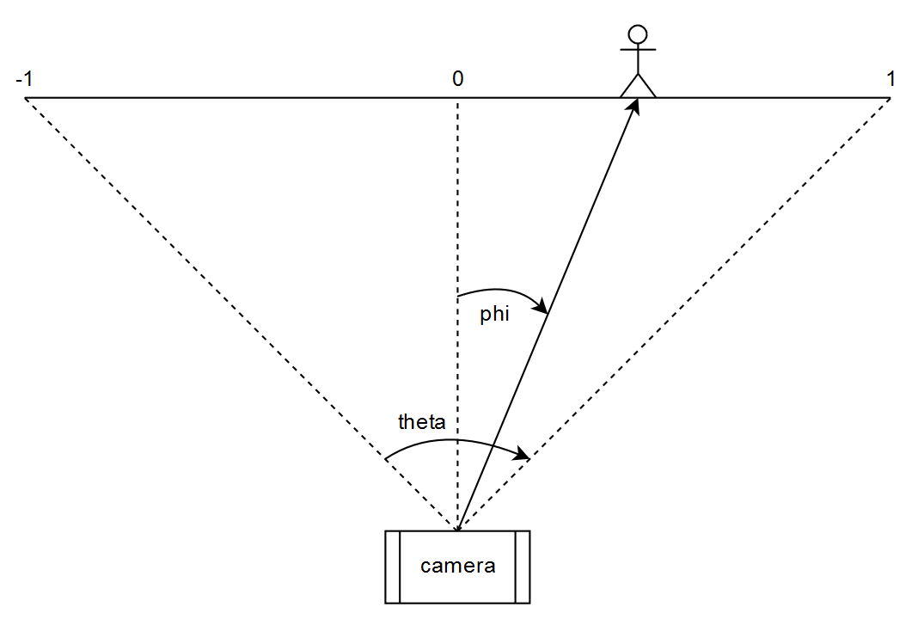
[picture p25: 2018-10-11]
Thesis Report/methodology/pixel_to_angle.PNG

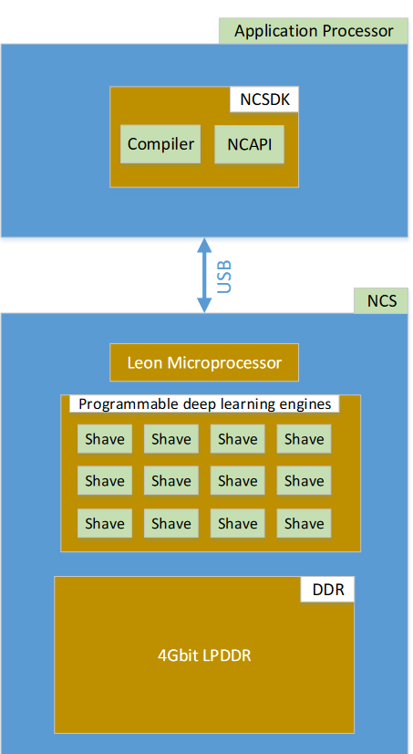
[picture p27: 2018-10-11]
Thesis Report/literature_review/NCS_internals.png

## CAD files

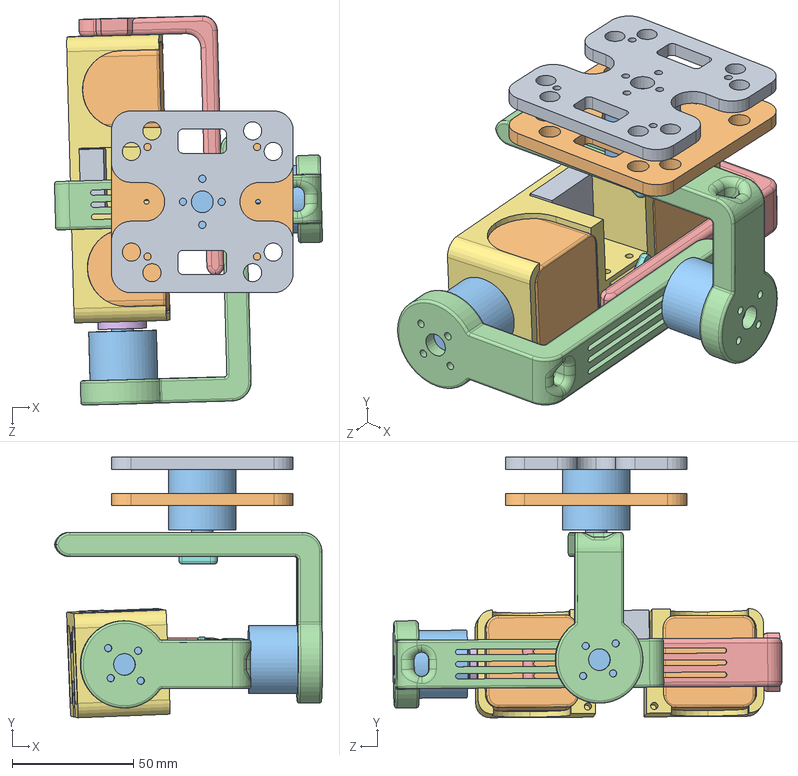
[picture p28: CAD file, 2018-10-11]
Gimbal design/Gimbal_assembly_2.SLDASM
110.6 x 107.5 x 160.4 mm
Plate_top
Plate_bottom
Motor_LD_power_2208 x 3
Roll_motor_bracket x 2
Camera_support_bracket
Motor_rotor_attachment
GoPro_mount
Motor_other_rotor_attachment x 2
RPi_camera
gopro_session_5 x 2

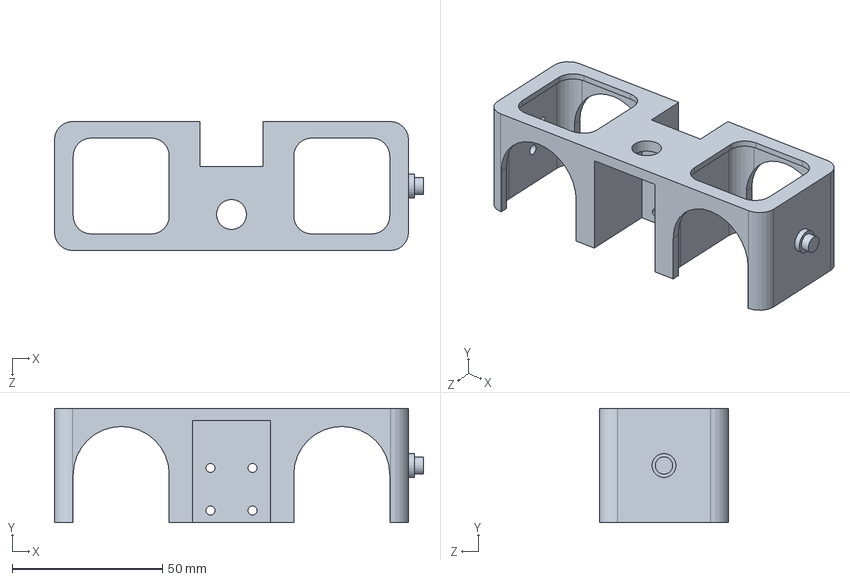
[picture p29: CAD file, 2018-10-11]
Gimbal design/GoPro_mount.SLDPRT
123.0 x 38.0 x 43.0 mm

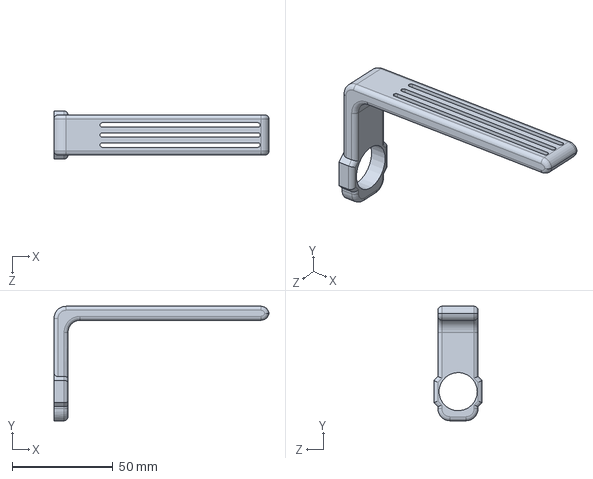
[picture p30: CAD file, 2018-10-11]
Gimbal design/Camera_support_bracket.SLDPRT
107.0 x 57.0 x 24.0 mm

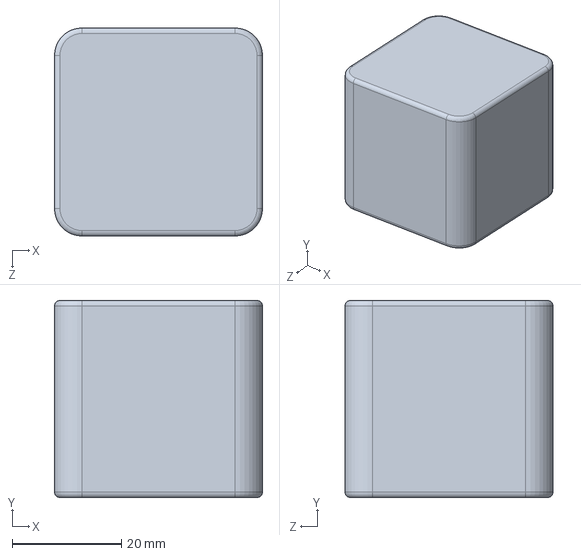
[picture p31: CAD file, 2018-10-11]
Gimbal design/gopro_session_5.SLDPRT
38.0 x 36.0 x 38.0 mm

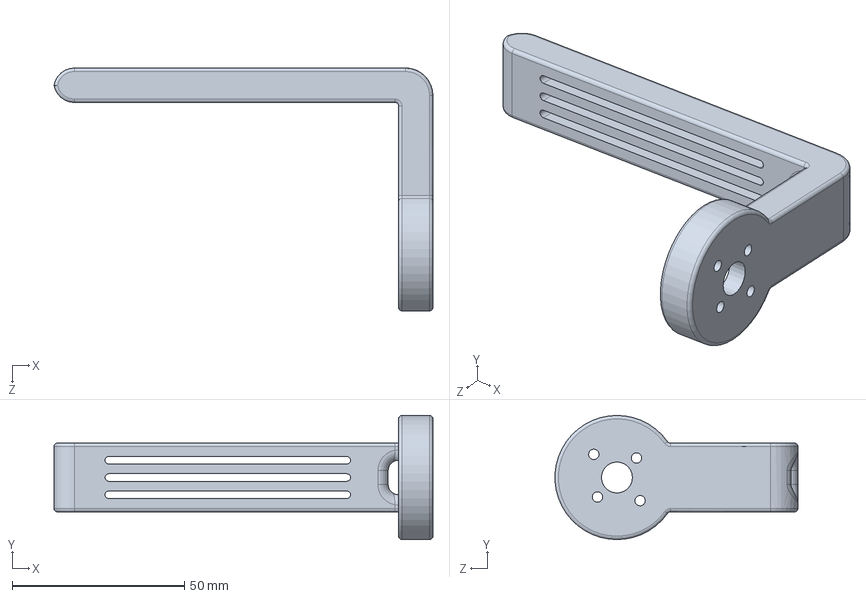
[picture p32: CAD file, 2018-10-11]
Gimbal design/Roll_motor_bracket.SLDPRT
109.9 x 36.0 x 70.5 mm

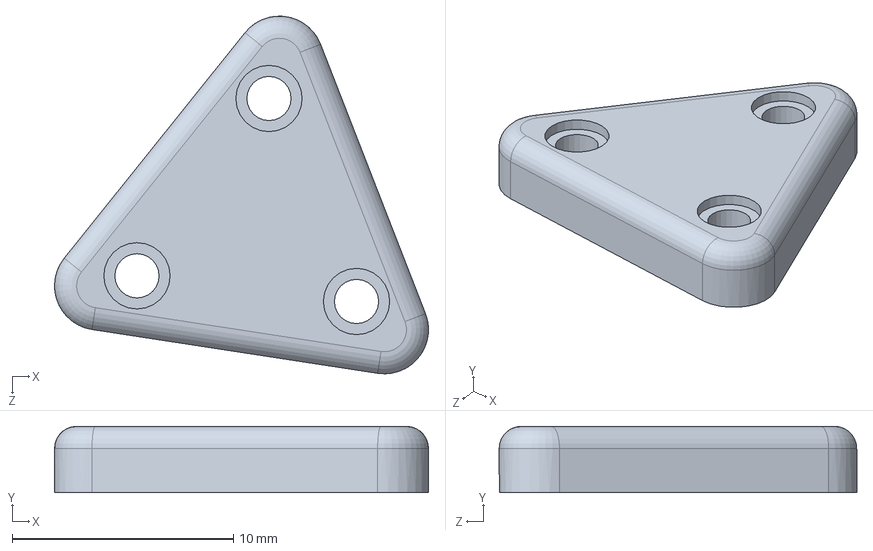
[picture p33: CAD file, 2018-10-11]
Gimbal design/Motor_other_rotor_attachment.SLDPRT
16.9 x 3.00 x 16.2 mm

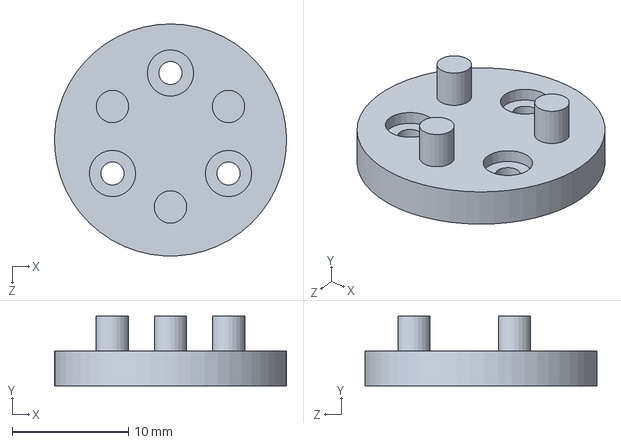
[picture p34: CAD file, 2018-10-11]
Gimbal design/Motor_rotor_attachment.SLDPRT
20.0 x 6.00 x 20.0 mm

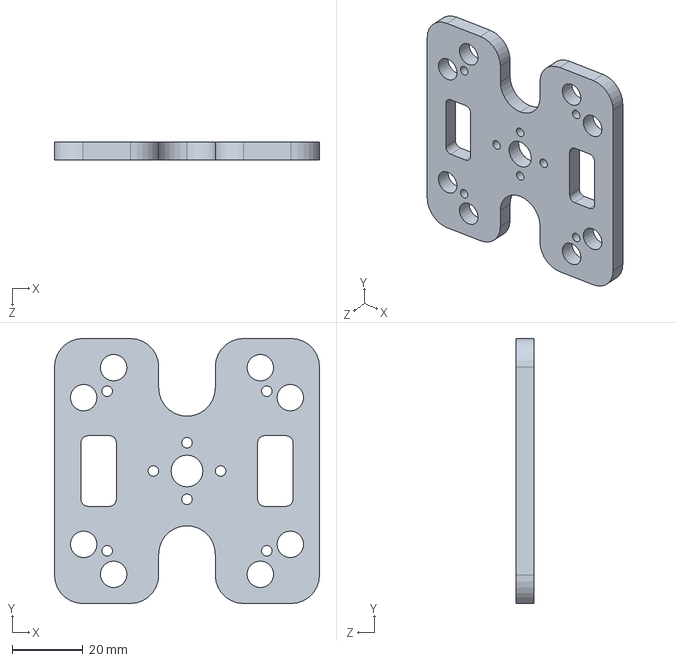
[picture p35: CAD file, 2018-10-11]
Gimbal design/Plate_top.SLDPRT
75.0 x 75.0 x 5.00 mm

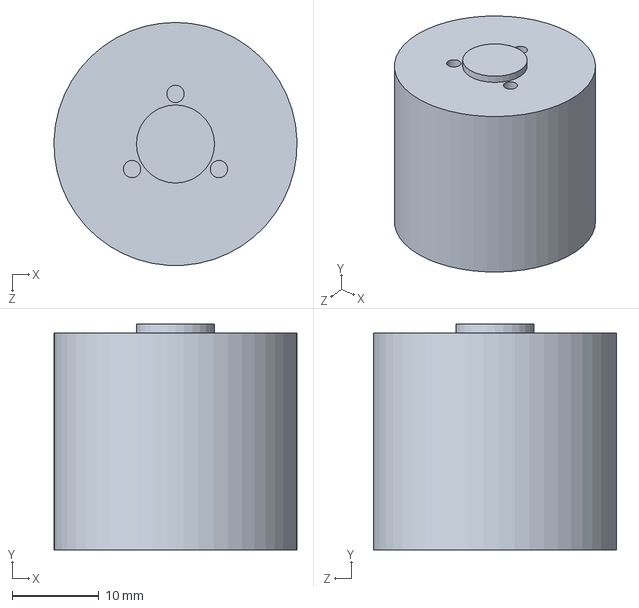
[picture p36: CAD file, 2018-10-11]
Gimbal design/Motor_LD_power_2208.SLDPRT
28.0 x 26.0 x 28.0 mm

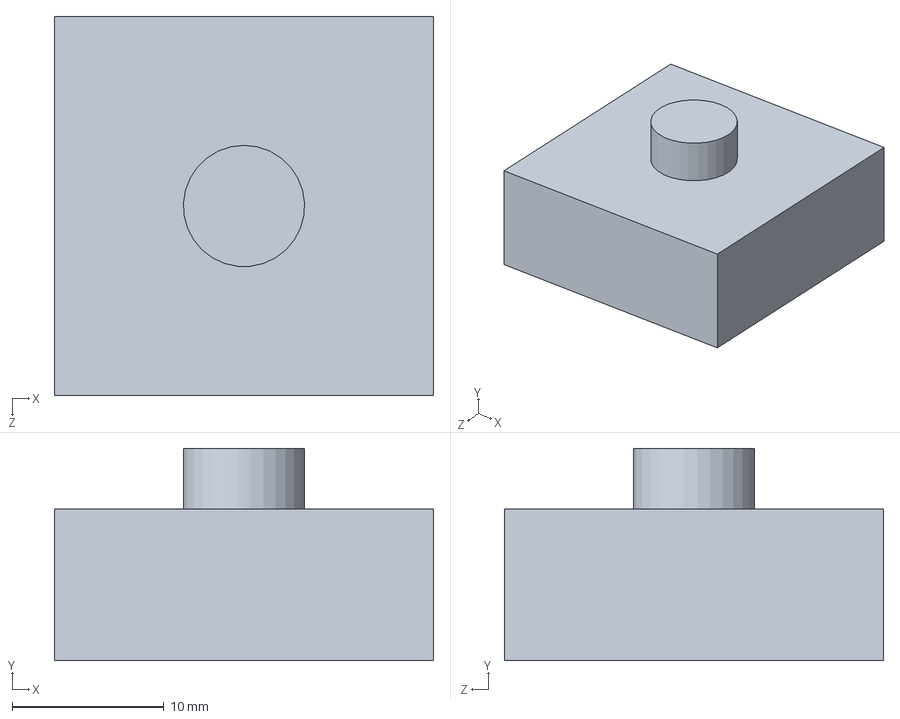
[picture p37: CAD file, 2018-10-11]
Gimbal design/RPi_camera.SLDPRT
25.0 x 14.0 x 25.0 mm

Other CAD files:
Gimbal design/Plate_bottom.SLDPRT

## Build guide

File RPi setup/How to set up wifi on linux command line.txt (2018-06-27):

### HOW TO GET UCT WIFI WORKING ON LINUX VIA COMMAND LINE:

> nano /etc/wpa_supplicant/wpa_supplicant.conf

In wpa_supplicant.conf, change the contents to the lines between the %%:

%%
ctrl_interface=DIR=/var/run/wpa_supplicant GROUP=netdev
update_config=1
country=ZA

network={
	ssid="eduroam"
	scan_ssid=1
	key_mgmt=WPA-EAP
	eap=PEAP
	group=CCMP TKIP
	identity="STUDENT_NUMBER_HERE@wf.uct.ac.za"
	password="PASSWORD_HERE"
	ca_cert="/home/pi/.cat_installer/ca.pem"
	domain_suffix_match="uct.ac.za"
	phase2="auth=MSCHAPV2"
}

%%

Reboot using
> shutdown -r now

Check whether the wifi is working by pinging Google's servers:
> ping 8.8.8.8
If you get a response (some writing with a number in milliseconds) then all should be good

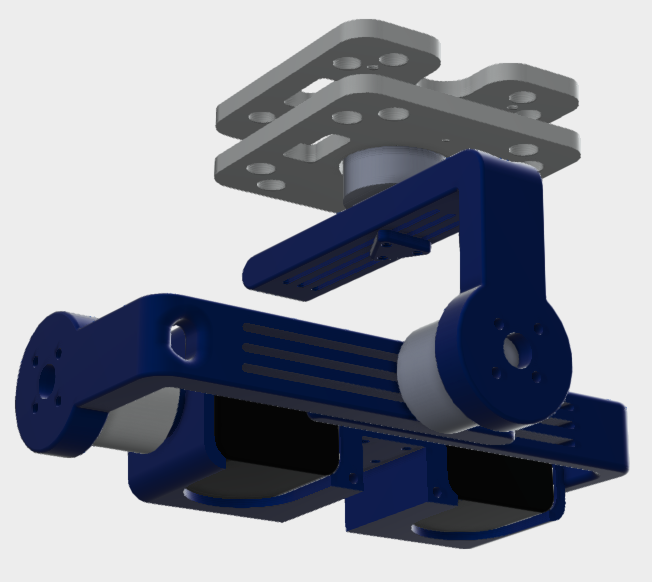
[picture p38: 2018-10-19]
Thesis Report/methodology/assembled_render_behind.PNG

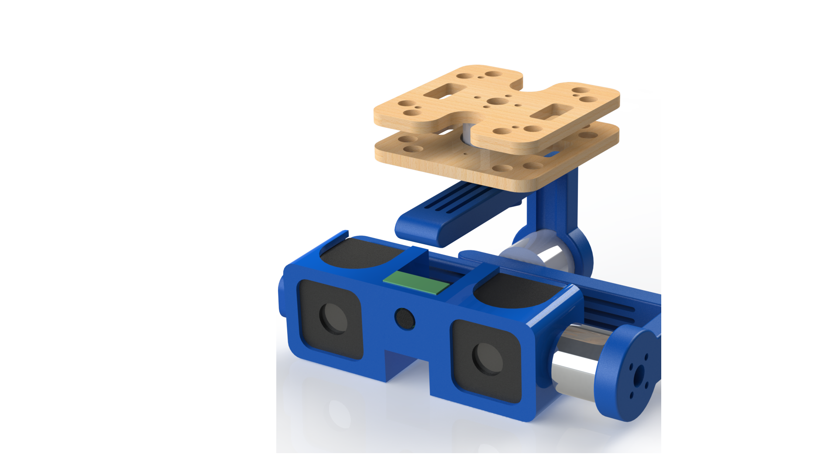
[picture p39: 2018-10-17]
Thesis Report/methodology/assembled_render.png

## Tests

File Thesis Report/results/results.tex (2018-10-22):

\chapter{Results}\label{chap:results}

Once everything had been put together, tests were done to conclude whether the system met the requirements of the researchers.

The setup was as follows: the tracking system was loaded with the Raspberry Pi camera and two GoPro Hero Sessions, one of which was set to record. Another GoPro was placed next to the system, and set to wide angle mode - this acted as a control when comparison was necessary. Since the tests were oriented towards video footage, it is advised to watch a few sample recordings to get a feel for how the system operates. \href{https://www.youtube.com/watch?v=NjCOmwhG3zo}{Click this sentence for a link to the authors submission into the SAIEEE NSPC}, and \href{https://youtu.be/Oea_mKTjV5U}{click this sentence for a link to see two videos which compare the stationary and tracking cameras}.

Due to time constraints, the tests performed were done on humans in a laboratory.

\section{Testing whether the system can track an object}
What follows is a series of tests which demonstrate the scenarios in which the tracker succeeds (or fails) to work.

\subsection{Aiming at a stationary object}
The first test demonstrated that the system can locate and rotate towards an object in a complex environment. While this initially resulted in the gimbal oscillating around the object, once the timing issues had been fixed, the system was able to smoothly aim at the object before stopping entirely.

The system was unphased by the movement of other objects in the frame, such as a pushed chair.

\subsection{Tracking a slow moving object}
Next, the system was made to track an object moving in a slow, straight line. The camera would track the object in a slightly jerky fashion for the first two seconds, before correctly estimating the objects velocity and tracking it smoothly. During steady state, the camera lagged behind a walking-pace object with an angle of approximately 10\textdegree, depending on the velocity of the object and the distance to the camera.

\begin{figure}[h!]
  \centering
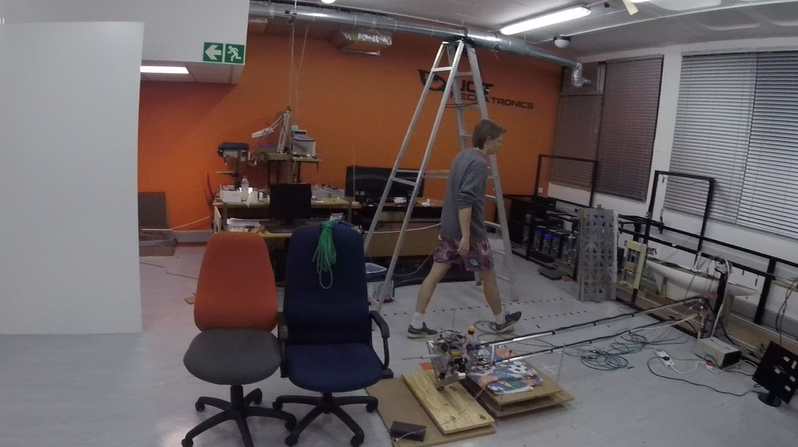
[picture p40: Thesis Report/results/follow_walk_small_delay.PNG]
  
  \caption{\label{fig:follow_walk_small_delay}A photo of the system tracking a human walking at a slow pace.}
\end{figure}

\subsection{Tracking a fast moving object}
A test was done to see whether the system can track an object moving at higher velocities. It failed under either of two conditions:

If the object accelerated too quickly, the camera would sometimes fail to estimate the objects velocity before it left the frame and then rotate slowly towards the direction that the object had last been seen in.

If the object's velocity was too high, the gimbal would fail to rotate fast enough and again lose sight of the object. However, if the object stopped or slowed down out of frame, the system would find it and start tracking properly again.

\subsection{Tracking a crouching or elevated object}
The system could adequately track an object at higher or lower pitch levels. Since more smoothing was applied to the Kalman Filter estimating the pitch of the object, the gimbal would take slightly longer to change its pitch than it would to change its yaw.

\subsection{Tracking partially hidden objects}
Objects which were partially hidden (for example, a human behind a large chair or workspace divider) could still be adequately tracked. However, this stopped working when only the face of the tracked object was visible from 5 meters away.

\section{Testing the maximum angular tracking range}
Moving in a circle around the tracker empirically showed that the yaw rotation range was 175\textdegree, while the pitch could track from approximately $-$45\textdegree\ (before the system itself started obscuring the object) to 90\textdegree{}, with 0\textdegree{} being horizontal.

A GoPro Hero Session camera has a maximum field of view of 122\textdegree{} if set to the highest setting.

%\begin{figure}
%	\centering
%	\animategraphics[loop,autoplay,width=\textwidth]{12}{./tracking_cam_test_7/smaller_img}{0}{53}
%\end{figure}

\section{Testing the angular distortion effects}
To test and show the effects of distortion, two pictures taken in the same moment in time are shown below, in Figures~\ref{fig:distorted_gopro} and \ref{fig:less_distorted_gopro}.

\begin{figure}[h!]
  \centering
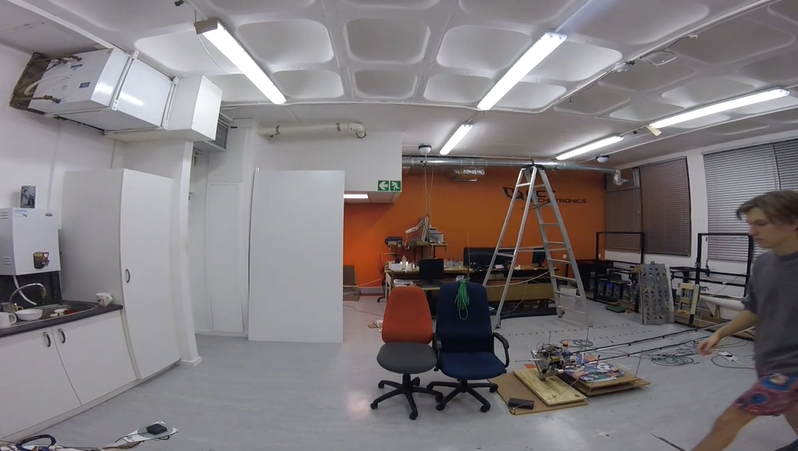
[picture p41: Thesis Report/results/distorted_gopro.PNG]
  
  \caption{\label{fig:distorted_gopro}Photo from the stationary camera showing the distortions due to the cameras wide-angle mode.}
\end{figure}

\begin{figure}[h!]
  \centering
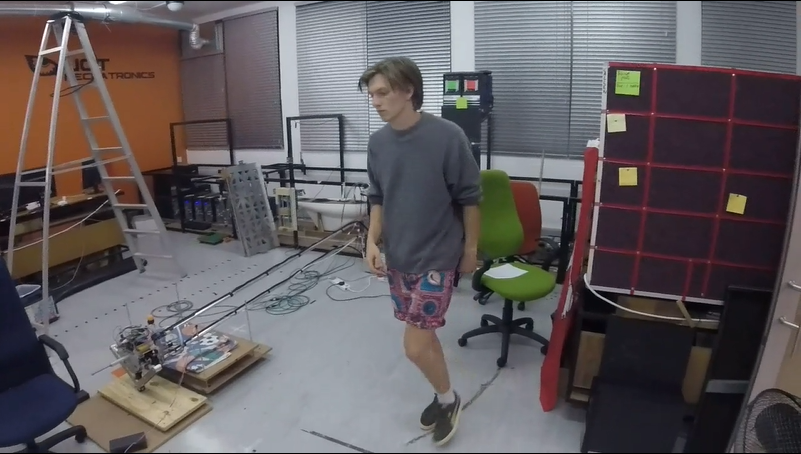
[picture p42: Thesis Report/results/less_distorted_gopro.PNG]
  
  \caption{\label{fig:less_distorted_gopro}Photo from the rotating camera showing less distortion.}
\end{figure}

The distortion effects are easier to see when looking at straight lines (made to look curved) in the edges and corners of the image.

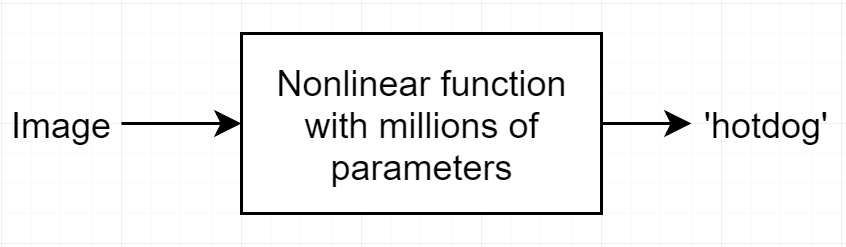
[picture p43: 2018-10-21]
Thesis Report/literature_review/img_to_result.PNG

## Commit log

2018-06-27 Add .xlsx files
    Used to keep Gantt chart backed up
    [Thesis Project - Gantt Chart.xlsx]
2018-07-19 Fix wifi, update setup guide, output MVNC graph file
    [Thesis Project - Gantt Chart.xlsx]
2018-08-15 Long overdue update
    [Thesis Project - Gantt Chart.xlsx]
2018-08-15 Clean up live classifier script
    Still need to take away irrelevant command line arguments, and make the thing run at a constant speed (eg. 10 Hz)
2018-09-05 Add tex docs, notebooks, start of main code
    [Thesis Project - Gantt Chart.xlsx]
2018-09-12 Add gimbal mechanical design
    [Camera_support_bracket.SLDPRT, Gimbal_assembly.SLDASM, Gimbal_assembly_2.SLDASM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]
2018-09-12 Updated gimbal. Not yet v2 ready
    [Motor_other_rotor_attachment.SLDPRT]
2018-09-13 Gimbal v2 done, need to check it
    [Camera_support_bracket.SLDPRT, Gimbal_assembly.SLDASM, Gimbal_assembly_2.SLDASM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]
2018-09-14 Add some work on thesis doc
    [ELO Supervision Tracking Form-EEE4022-2017.xls, Thesis Project - Gantt Chart.xlsx]
2018-09-18 Some work on image_classifier.ipynb. Currently breaks the pi sometimes :/
2018-09-18 Small updates to gimbal design v2
    [Gimbal_assembly_2.SLDASM, Motor_other_rotor_attachment.SLDPRT, Roll_motor_bracket.SLDPRT]
2018-09-18 Update Gantt chart and sources.txt
    [Thesis Project - Gantt Chart.xlsx]
2018-09-19 Quick commit in case the pi crashes. Fixed checksum issue in gimbal_control.ipynb
2018-09-27 Work on paper + EKF
    [ELO Supervision Tracking Form-EEE4022-2017.xls, Thesis Project - Gantt Chart.xlsx]
2018-09-27 Start work on threading image_classifier.ipynb
2018-09-28 Image classifier working at ~5 Hz
2018-10-01 Logging data to csv for EKF; debugging work on concurrency
    [logged_data_1.csv]
2018-10-02 Add logged data for offline EKF
    [logged_data_2.csv, logged_data_3.csv]
2018-10-03 Updated debug and switched pitch angle to up=pos
2018-10-08 Updated and submitted ELO tracking forms
    [ELO Supervision Tracking Form-EEE4022-2018.xls]
2018-10-09 Finally fixed camera FOV problem (but latency is cray)
2018-10-10 Added materials to gimbal parts
    [Camera_support_bracket.SLDPRT, Gimbal_assembly_2.SLDASM, GoPro_mount.SLDPRT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]
2018-10-15 Deleting old logged data
    [logged_data_1.csv, logged_data_2.csv]
2018-10-16 Added save method to EL and tuned KF pitch/yaw offline
2018-10-19 Increased yaw limits, decreased pitch limits
2018-10-22 Expanded Gantt chart to full view. It wasn't used much in the last few weeks of the project
    [Thesis Project - Gantt Chart.xlsx]
